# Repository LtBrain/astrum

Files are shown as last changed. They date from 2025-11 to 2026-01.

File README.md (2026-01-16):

# **ASTRUM**
Astrum (2)  
Astrum is a full robot designed for Science Olympiad's Robot Tour Event (2025-2026). It is designed to follow a predetermined path to navigate a maze and manipulate a water bottle to specific points on the floor. It is equipped with dual GA25 motors, a controller board (Aero), wheel encoders and an IMU to keep track of orientation. These features allow Astrum to quickly navigate the predetermined path efficiently and accurately with a PID loop controlling robot turning and motor speed.  
<br><br>
Astrum was created for the purpose of "placing" at the Mid-Hudson Valley Regionals competition, and to secure Nanuet a medal. Additionally, it serves as an educational tool for other students interested in robotics and control systems. It is able to be programmed in C, as well as Arduino, making it very effective for learning embedded software. This is also practice for myself, testing my design skills with both the hardware, and efficiently programming software to run on said board.  
  
## PCB
  

## Wiring Diagram 
wirediagram drawio
  
## BOM
Here's the BOM:  

 |Item #|Name                                       |Link                                     |Amount               |Cost   |
|------|-------------------------------------------|-----------------------------------------|---------------------|-------|
|1     |PCB + Assembly + Shipping                  |jlcpcb.com                               |1 order (2 boards)   |$170.40|
|2     |25GA-370 Brushed Motors                    |https://www.aliexpress.us/item/3256807346702379.html?|2                    |$12.94 |
|3     |Alinan AS5600 Encoder Boards               |https://www.aliexpress.us/item/3256809413529733.html?                              |1 pack (5 Encoders)  |$6.09 |
|4     |STEMMA QT to Male Header Cable             |https://www.aliexpress.com/item/3256805529535394.html?    |2                    |$2.78 |
|5     |2800 mAh AA NIMH Batteries                 |https://www.aliexpress.com/item/3256808440628751.html?                     |1 pack (12 Batteries)|$7.67 |
|6     |4 x AA Battery Holder                      |https://www.aliexpress.com/item/2255799895517935.html?     |2                    |$1.90  |
|7     |M3 16mm SHCS                               |M3 SHCS link                             |50                   |Paid by me  |
|8     |BaneBots T6 Wheel, 2-3/8" x 0.6", Hub Mount|https://banebots.com/t61p-242bp/         |2                    |$6.60  |
|9     |MF128ZZ Bearings - 8mm x 12mm x 3.5mm      |https://www.aliexpress.com/item/3256807566213882.html?                      |1 pack (8 bearings) |$6.10  |
|10    |Polulu 1/2 Inch Metal Ball Caster Wheels   |https://www.aliexpress.com/item/3256808387820251.html?     |4                    |$4.63 |
|11    |Pin Headers                                |https://www.aliexpress.com/item/2255800801798474.html?    |10                    |$1.69  |
|      |                                           |                                         |                     |Total: |
|      |                                           |                                         |                     |$220.80|
 
https://github.com/LtBrain/astrum/blob/main/Astrum%20BOM%20-%20Sheet1.csv

This covers the total sum of all the major parts.  

There is a more in depth BOM for the PCB assembly components itself: [BOM-astrum-JLCPCB Assembly Order.xls](https://github.com/user-attachments/files/23870804/BOM-astrum-JLCPCB.Assembly.Order.xls)  
  
REVIEWERS: Do note that I am aware of the high PCB fabrication costs + shipping, but this is the cheapest I could find it for (at JLCPCB). Additionally, the global standard direct shipping option will not work for this board. Sadly, JLCPCB requires the purchase to be under 59.99 dollars, which this board exceeds. This is why it got so expensive. Also do note that I have optimized my BOMs to be as cheap as possible to lower the amount of money spent by Hackclub.

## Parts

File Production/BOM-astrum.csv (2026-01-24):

Comment | Designator | Footprint | LCSC | Quantity
100nF | C11,C15,C16,C17,C19,C21,C4,C5,C6 | C_0603_1608Metric | C14663 | 9
100nF | C22 | C_0402_1005Metric | C1525 | 1
10k | R10,R8,R9 | R_0603_1608Metric | C25804 | 3
18pF | C7,C8 | C_0603_1608Metric | C1647 | 2
1uF | C12,C13,C9 | C_0603_1608Metric | C15849 | 3
2.2uF | C2 | C_0402_1005Metric | C12530 | 1
2.2uF | C1 | C_0603_1608Metric | C23630 | 1
22uF | C18,C20 | CP_Elec_4x5.4 | C3356 | 2
25mHz | Y2 | Crystal_SMD_3225-4Pin_3.2x2.5mm | C9006 | 1
30k | R3,R4 | R_0603_1608Metric | C22984 | 2
4.7k | R6 | R_0603_1608Metric | C23162 | 1
4.7uF | C10,C3 | C_0603_1608Metric | C19666 | 2
5.1k | R1,R2 | R_0603_1608Metric | C23186 | 2
Conn_01x04_MountingPin | J5,J6 | JST_SH_SM04B-SRSS-TB_1x04-1MP_P1.00mm_Horizontal | C160404 | 2
DRV8871DDA | U8,U9 | Texas_HTSOP-8-1EP_3.9x4.9mm_P1.27mm_EP2.95x4.9mm_Mask2.4x3.1mm_ThermalVias | C75864 | 2
LDL212PV33R | U2 | DFN_V33R_STM | C2969892 | 1
LSM6DSR | U6 | LGA_M6DSR_STM | C784817 | 1
Micro_SD_Card | J2 | microSD_HC_Wuerth_693072010801 | C5912397 | 1
NSR0530HT3G | D3 | D_SOD-323 | C191023 | 1
STM32H523CEUx | U1 | QFN-48-1EP_7x7mm_P0.5mm_EP5.6x5.6mm | C26082147 | 1
TS-1088-AR02016 | SW1,SW2 | SW-SMD_L3.9-W3.0-P4.45 | C720477 | 2
USBLC6-2SC6 | U3 | SOT-23-6 | C7519 | 1
USB_C_Receptacle_USB2.0_16P | J1 | USB_C_Receptacle_JAE_DX07S016JA1R1500 | C3197885 | 1
W25Q32JVSS | U4 | SOIC-8_5.3x5.3mm_P1.27mm | C97521 | 1
Conn_01x10_Pin | J8 | PinHeader_1x10_P2.54mm_Vertical |  | 1
Conn_01x10_Pin | J7 | PinHeader_1x10_P2.54mm_Vertical |  | 1
Conn_01x05_Pin | J10 | PinHeader_1x05_P2.54mm_Vertical |  | 1
Screw_Terminal_01x02 | J11 | TerminalBlock_bornier-2_P5.08mm |  | 1
Screw_Terminal_01x02 | J3 | TerminalBlock_bornier-2_P5.08mm |  | 1
Conn_01x05_Pin | J9 | PinHeader_1x05_P2.54mm_Vertical |  | 1

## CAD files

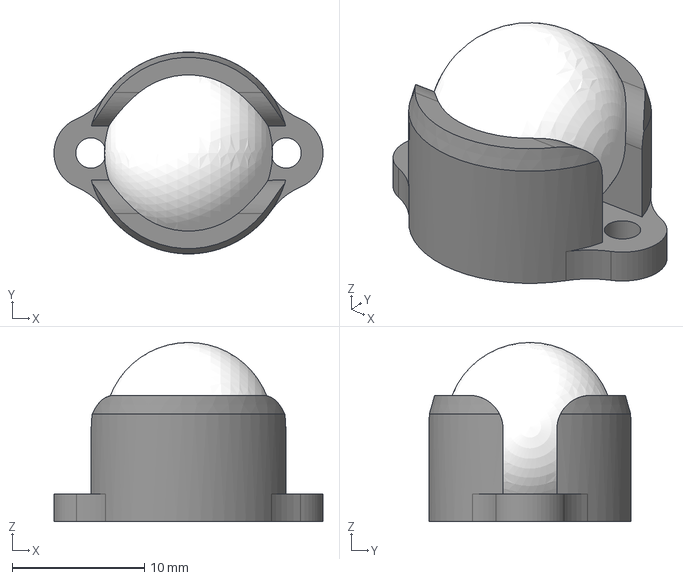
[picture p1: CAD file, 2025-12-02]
Production/3D Printed Parts/Motor_Mount.step
20.3 x 15.2 x 13.5 mm

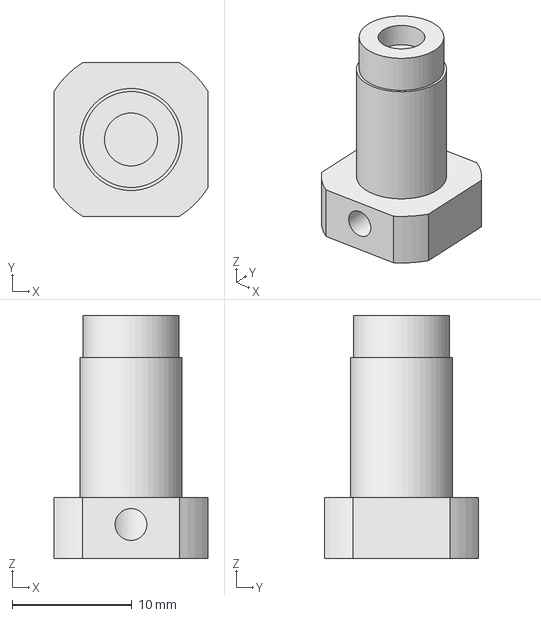
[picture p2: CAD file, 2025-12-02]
Production/3D Printed Parts/Motor_Hub.step
12.8 x 12.8 x 20.3 mm

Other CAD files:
Production/3D Printed Parts/Front_Plate.step
Production/3D Printed Parts/Bottom_Plate.step
Production/3D Printed Parts/Sensor_Hub.step
Production/3D Printed Parts/Wall_Plate.step

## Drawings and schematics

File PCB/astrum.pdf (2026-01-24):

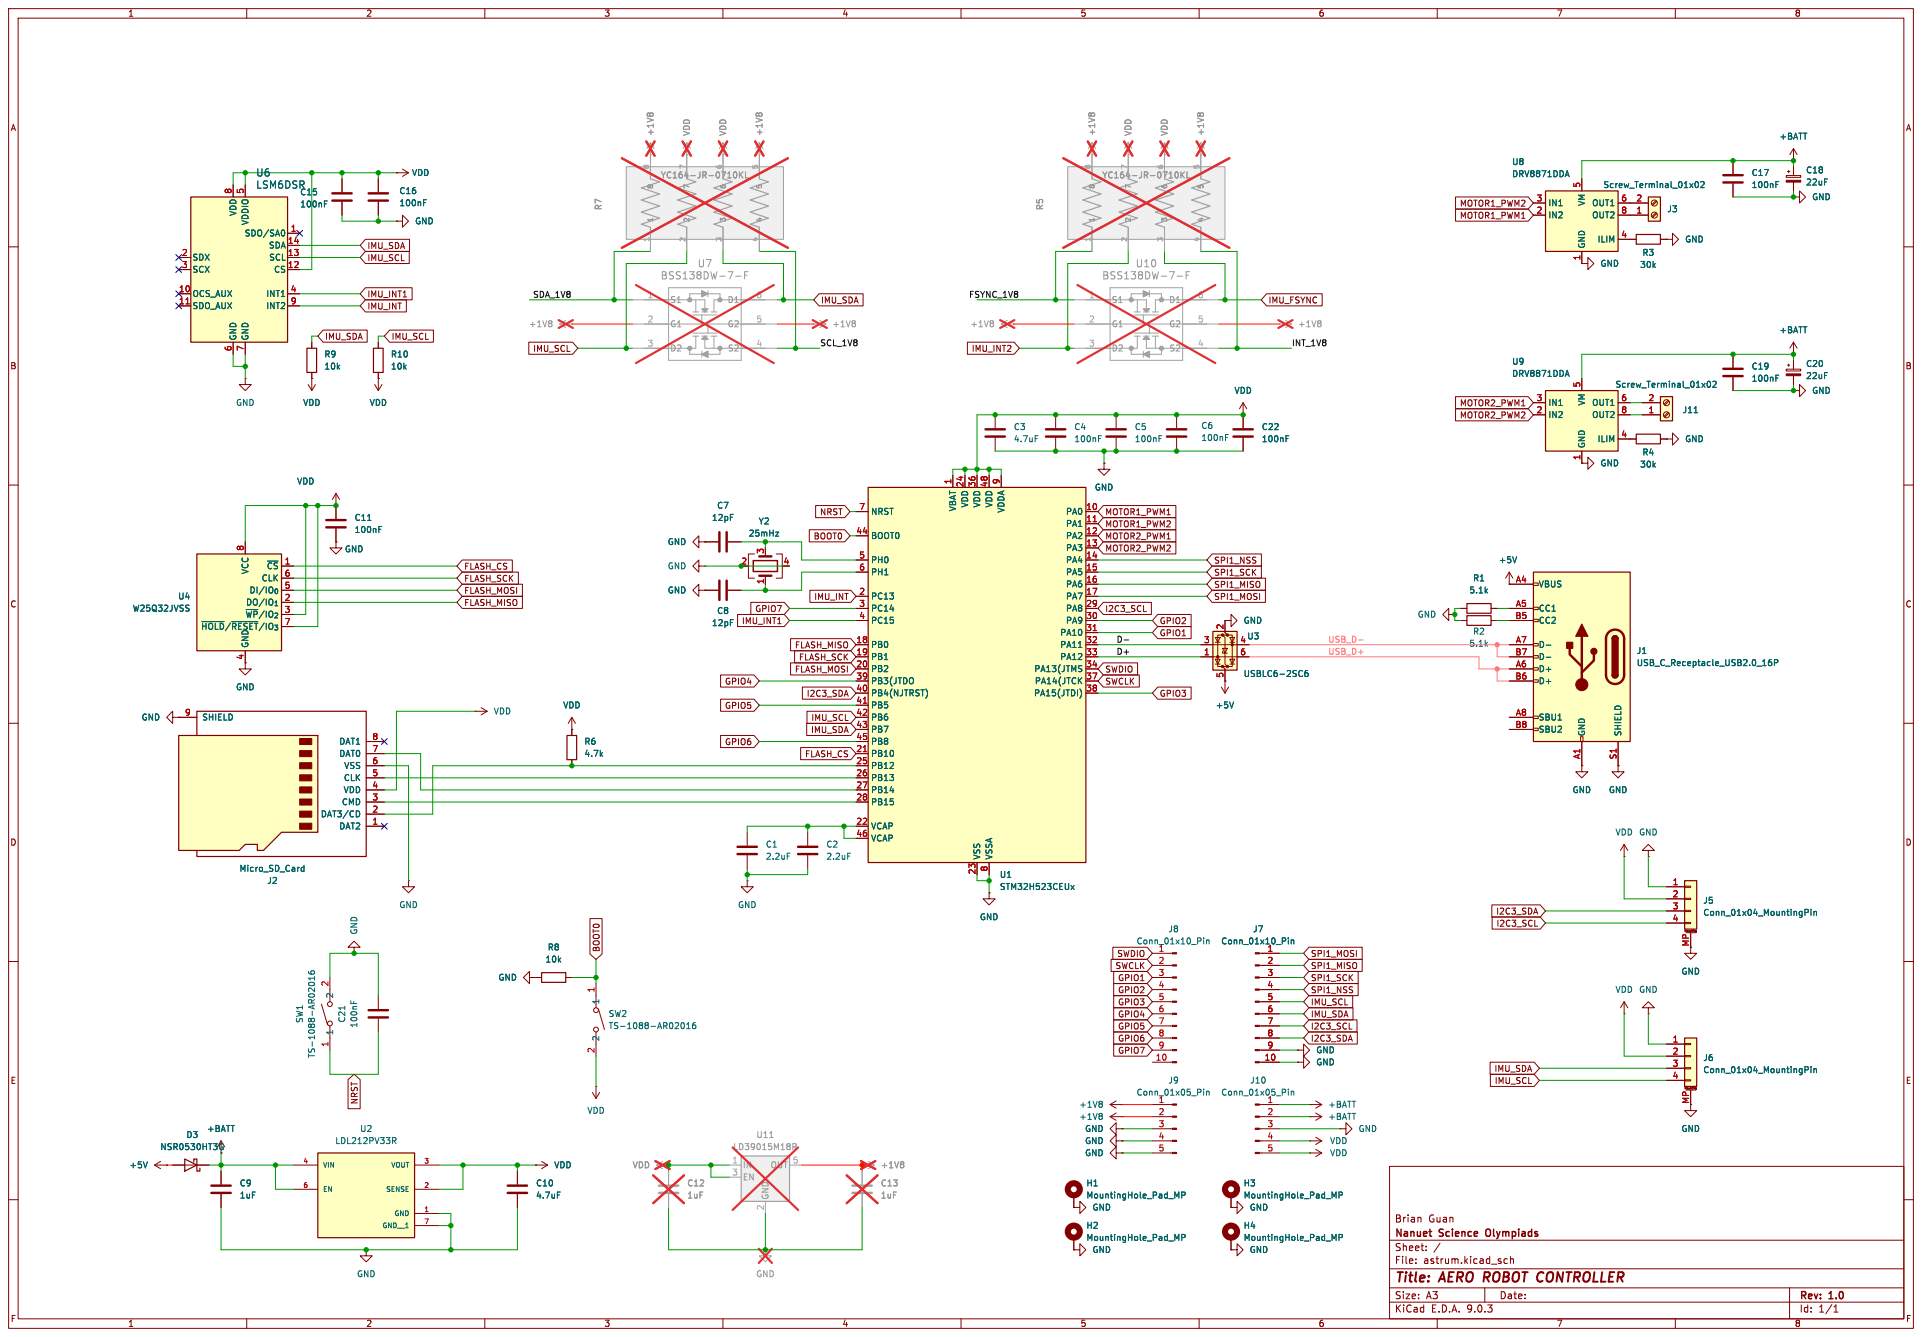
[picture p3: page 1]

7 SDO/SA0 1 SDA 14 SCL 13 CS 12

1 VDD 24 VDD 36 VSS 23 VDD 48 VSSA

9 PA0 10 PA1 11 PA2 12 PA3 13 PA4 14 PA5 15 PA6 16 PA7 17 PA8 29 PA9 30 PA10 31 PA11 32 PA12 33 PA13(JTMS 34 PA14(JTCK 37 PA15(JTDI) 38GND GND GND GND

~{CS}1 CLK 6 DI/IO_{0}5 DO/IO_{1}2 ~{WP}/IO_{2} 3 ~{HOLD}/~{RESET}/IO_{3} 7 VCC

Id: 1/1 Title: AERO ROBOT CONTROLLER

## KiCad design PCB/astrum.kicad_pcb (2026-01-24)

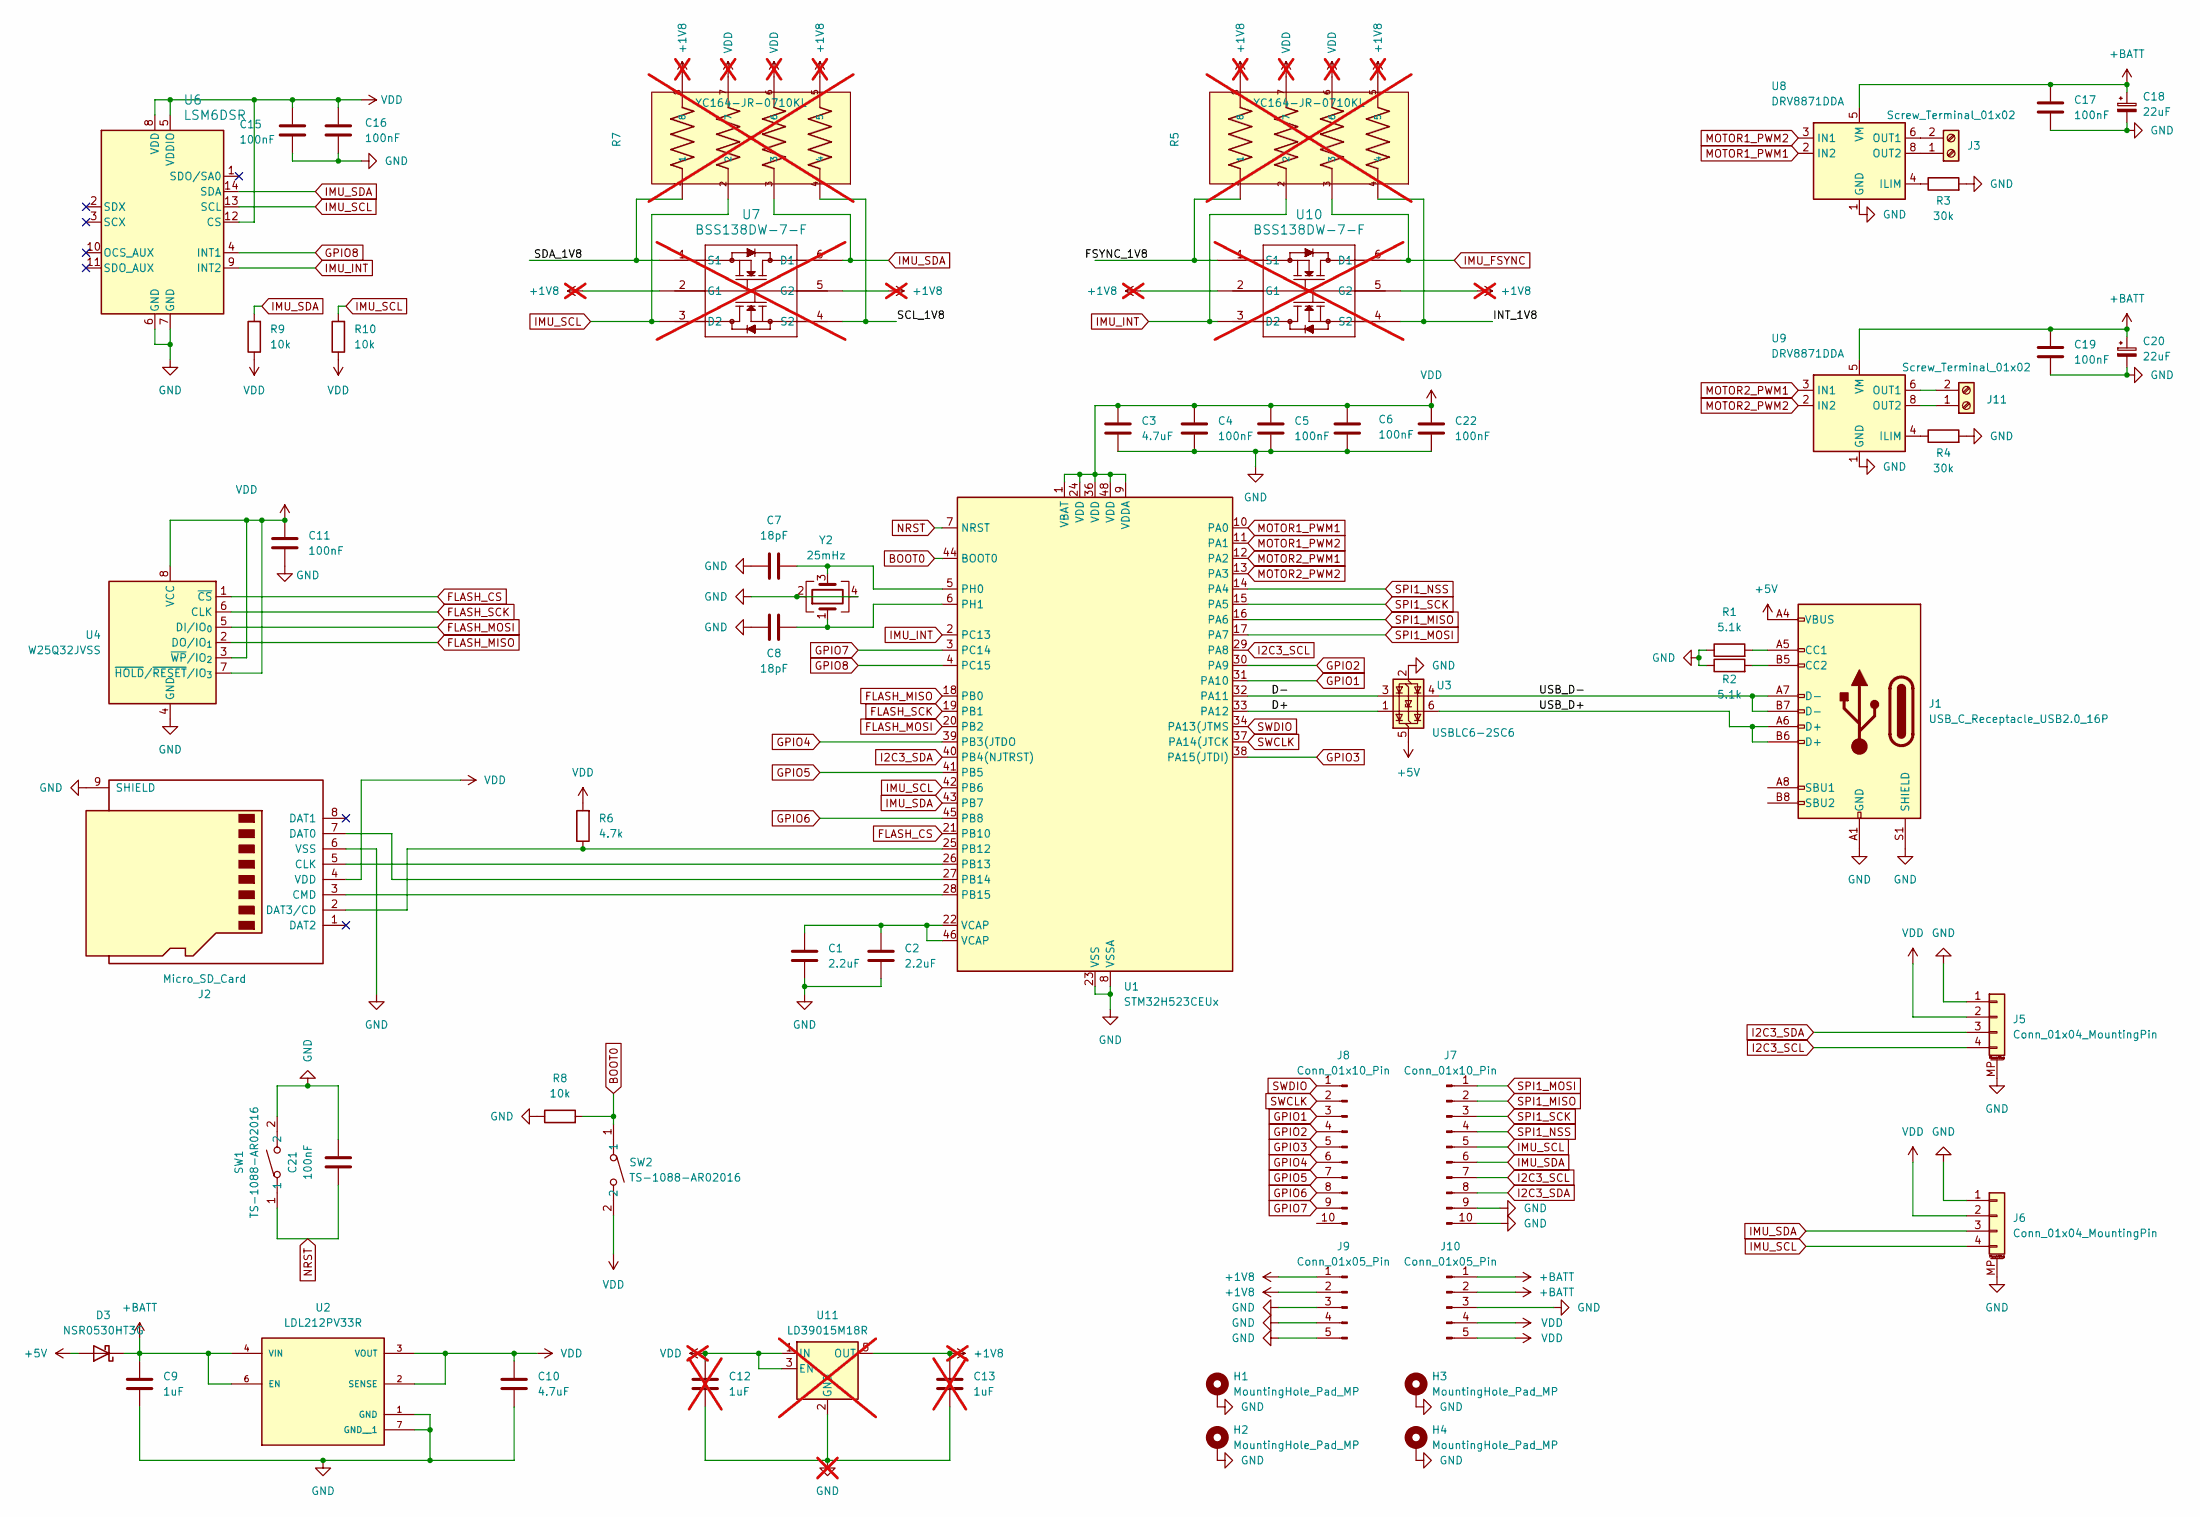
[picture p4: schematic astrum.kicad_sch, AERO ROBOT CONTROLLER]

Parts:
C1: 2.2uF; C_0603_1608Metric
C2: 2.2uF; C_0402_1005Metric
C3, C10: 4.7uF; C_0603_1608Metric
C4, C5, C6, C11, C15, C16, C17, C19, C21: 100nF; C_0603_1608Metric
C7, C8: 18pF; C_0603_1608Metric
C9: 1uF; C_0603_1608Metric
C12, C13: 1uF; C_0603_1608Metric; not fitted
C18, C20: 22uF; CP_Elec_4x5.4
C22: 100nF; C_0402_1005Metric
D3: NSR0530HT3G; D_SOD-323
H1, H2, H3, H4: MountingHole_Pad_MP; MountingHole_2.2mm_M2_ISO7380_Pad
J1: USB_C_Receptacle_USB2.0_16P; USB_C_Receptacle_JAE_DX07S016JA1R1500
J2: Micro_SD_Card; microSD_HC_Wuerth_693072010801
J3, J11: Screw_Terminal_01x02; TerminalBlock_bornier-2_P5.08mm
J5, J6: Conn_01x04_MountingPin; JST_SH_SM04B-SRSS-TB_1x04-1MP_P1.00mm_Horizontal
J7, J8: Conn_01x10_Pin; PinHeader_1x10_P2.54mm_Vertical
J9, J10: Conn_01x05_Pin; PinHeader_1x05_P2.54mm_Vertical
R1, R2: 5.1k; R_0603_1608Metric
R3, R4: 30k; R_0603_1608Metric
R5, R7: YC164-JR-0710KL; RESCAXE80P320X160X70-8N; PARTREV 9; not fitted
R6: 4.7k; R_0603_1608Metric
R8, R9, R10: 10k; R_0603_1608Metric
SW1, SW2: TS-1088-AR02016; SW-SMD_L3.9-W3.0-P4.45; LCSC Part C720477
U1: STM32H523CEUx; QFN-48-1EP_7x7mm_P0.5mm_EP5.6x5.6mm
U2: LDL212PV33R; DFN_V33R_STM; PARTREV 5
U3: USBLC6-2SC6; SOT-23-6
U4: W25Q32JVSS; SOIC-8_5.3x5.3mm_P1.27mm
U6: LSM6DSR; LGA_M6DSR_STM
U7, U10: BSS138DW-7-F; SOT363_DIO; not fitted
U8, U9: DRV8871DDA; Texas_HTSOP-8-1EP_3.9x4.9mm_P1.27mm_EP2.95x4.9mm_Mask2.4x3.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
U11: LD39015M18R; SOT-23-5; not fitted
Y2: 25mHz; Crystal_SMD_3225-4Pin_3.2x2.5mm

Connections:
+1V8: C13.1, J9.1, J9.2, R5.5, R5.8, R7.5, R7.8, U7.2 (G1), U7.5 (G2), U10.2 (G1), U10.5 (G2), U11.5 (OUT)
+5V: D3.2 (A), J1.A4 (VBUS), J1.A9 (VBUS), J1.B4 (VBUS), J1.B9 (VBUS), U3.5 (VBUS)
+BATT: C9.1, C17.1, C18.1, C19.1, C20.1, D3.1 (K), J10.1, J10.2, U2.4 (VIN), U2.6 (EN), U8.5 (VM), U9.5 (VM)
/D+: U1.33 (PA12), U3.1 (I/O1)
/D-: U1.32 (PA11), U3.3 (I/O2)
/FSYNC_1V8: R5.1, U10.1 (S1)
/INT_1V8: R5.4, U10.4 (S2)
/SCL_1V8: R7.4, U7.4 (S2)
/SDA_1V8: R7.1, U7.1 (S1)
/USB_D+: J1.A6 (D+), J1.B6 (D+), U3.6 (I/O1)
/USB_D-: J1.A7 (D-), J1.B7 (D-), U3.4 (I/O2)
BOOT0: R8.2, SW2.1, U1.44 (BOOT0)
FLASH_CS: U1.21 (PB10), U4.1 (~CS)
FLASH_MISO: U1.18 (PB0), U4.2 (DO/IO_{1})
FLASH_MOSI: U1.20 (PB2), U4.5 (DI/IO_{0})
FLASH_SCK: U1.19 (PB1), U4.6 (CLK)
GND: C1.2, C2.2, C3.2, C4.2, C5.2, C6.2, C7.1, C8.1, C9.2, C10.2, C11.2, C12.2, C13.2, C15.2, C16.2, C17.2, C18.2, C19.2, C20.2, C21.2, C22.2, H1.MP, H2.MP, H3.MP, H4.MP, J1.A1 (GND), J1.A12 (GND), J1.B1 (GND), J1.B12 (GND), J1.S1 (SHIELD), J2.6 (VSS), J2.9 (SHIELD), J5.1, J5.MP (MountPin), J6.1, J6.MP (MountPin), J7.9, J7.10, J9.3, J9.4, J9.5, J10.3, R1.1, R2.1, R3.2, R4.2, R8.1, SW1.2, U1.8 (VSSA), U1.23 (VSS), U1.35 (VSS), U1.47 (VSS), U1.49 (VSS), U2.1 (GND), U2.7 (GND__1), U3.2 (GND), U4.4 (GND), U6.6 (GND), U6.7 (GND), U8.1 (GND), U8.7 (GND), U8.9 (GND), U9.1 (GND), U9.7 (GND), U9.9 (GND), U11.2 (GND), Y2.2, Y2.4
GPIO1: J8.3, U1.31 (PA10)
GPIO2: J8.4, U1.30 (PA9)
GPIO3: J8.5, U1.38 (PA15(JTDI))
GPIO4: J8.6, U1.39 (PB3(JTDO)
GPIO5: J8.7, U1.41 (PB5)
GPIO6: J8.8, U1.45 (PB8)
GPIO7: J8.9, U1.3 (PC14)
GPIO8: U1.4 (PC15), U6.4 (INT1)
I2C3_SCL: J5.4, J7.7, U1.29 (PA8)
I2C3_SDA: J5.3, J7.8, U1.40 (PB4(NJTRST))
IMU_FSYNC: R5.3, U10.6 (D1)
IMU_INT: R5.2, U1.2 (PC13), U6.9 (INT2), U10.3 (D2)
IMU_SCL: J6.4, J7.5, R7.2, R10.2, U1.42 (PB6), U6.13 (SCL), U7.3 (D2)
IMU_SDA: J6.3, J7.6, R7.3, R9.2, U1.43 (PB7), U6.14 (SDA), U7.6 (D1)
MOTOR1_PWM1: U1.10 (PA0), U8.2 (IN2)
MOTOR1_PWM2: U1.11 (PA1), U8.3 (IN1)
MOTOR2_PWM1: U1.12 (PA2), U9.3 (IN1)
MOTOR2_PWM2: U1.13 (PA3), U9.2 (IN2)
NRST: C21.1, SW1.1, U1.7 (NRST)
unnamed: C1.1, C2.1, U1.22 (VCAP), U1.46 (VCAP)
unnamed: J1.A5 (CC1), R1.2
unnamed: J1.B5 (CC2), R2.2
unnamed: J2.5 (CLK), U1.26 (PB13)
unnamed: J2.3 (CMD), U1.28 (PB15)
unnamed: J2.7 (DAT0), U1.27 (PB14)
unnamed: J2.2 (DAT3/CD), R6.1, U1.25 (PB12)
unnamed: J3.1, U8.8 (OUT2)
unnamed: J3.2, U8.6 (OUT1)
unnamed: J11.1, U9.8 (OUT2)
unnamed: J11.2, U9.6 (OUT1)
unnamed: C7.2, U1.5 (PH0), Y2.3
unnamed: C8.2, U1.6 (PH1), Y2.1
unnamed: R3.1, U8.4 (ILIM)
unnamed: R4.1, U9.4 (ILIM)
SPI1_MISO: J7.2, U1.16 (PA6)
SPI1_MOSI: J7.1, U1.17 (PA7)
SPI1_NSS: J7.4, U1.14 (PA4)
SPI1_SCK: J7.3, U1.15 (PA5)
SWCLK: J8.2, U1.37 (PA14(JTCK)
SWDIO: J8.1, U1.34 (PA13(JTMS)
VDD: C3.1, C4.1, C5.1, C6.1, C10.1, C11.1, C12.1, C15.1, C16.1, C22.1, J2.4 (VDD), J5.2, J6.2, J10.4, J10.5, R5.6, R5.7, R6.2, R7.6, R7.7, R9.1, R10.1, SW2.2, U1.1 (VBAT), U1.9 (VDDA), U1.24 (VDD), U1.36 (VDD), U1.48 (VDD), U2.2 (SENSE), U2.3 (VOUT), U4.3 (~WP/IO_{2}), U4.7 (~HOLD/~RESET/IO_{3}), U4.8 (VCC), U6.5 (VDDIO), U6.8 (VDD), U6.12 (CS), U11.1 (IN), U11.3 (EN)

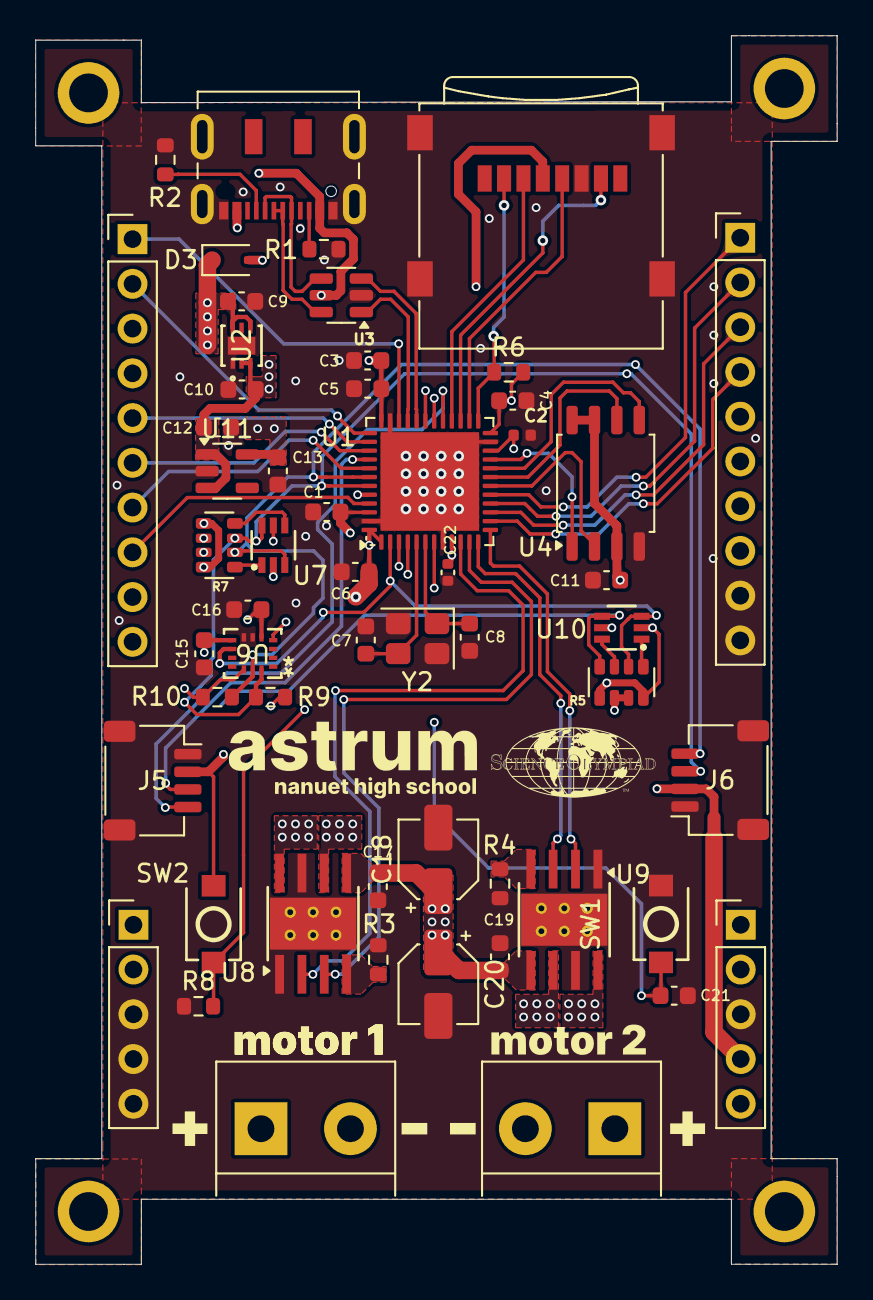
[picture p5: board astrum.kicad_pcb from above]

Board: 4 copper layers, 45.5 x 69.7 mm, 59 parts (0 on the bottom side), 58 nets.

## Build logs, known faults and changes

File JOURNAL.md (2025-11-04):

<!--
  ===================    !!READ THIS NOTICE!!   ====================
  DO NOT edit this file manually. Your changes WILL BE OVERWRITTEN!
  This journal is auto generated and updated by Hack Club Blueprint.
  To edit this file, please edit your journal entries on Blueprint.
  ==================================================================
-->

## 10/11/2025 9 PM - Planning and Schematic!  

I started out on my design with some rough knowledge on what I was going to use for this board. I had previously designed boards with the STM32H5 series, so I chose these as my microcontroller. This is a pretty solid choice for several reasons:

- 	Good documentation from STMicro (AN5711 comes with schematic diagrams)
- 	Lots of IO and interfaces to support the functionality on my board
- 	Is pretty cheap
-   Has lots of power, crucial for my control systems
-   STM32CubeMX makes configuration easy

With that determined, I began my KiCad project with the basic functionalities needed for the chip, such as decoupling capacitors and power rails. It was also at this time that I began to use CubeMX to determine which pins I should label for later peripheral usage, such as SPI, I2C and PWM from the timers: 

## 10/11/2025 10 PM - Power System & Drivers  

After sorting out the basic STM32 schematic, along with USB and storage, I decided to focus on my power supply. This board will primarily run on a 3v3 logic level, so I'll use the LDL212PV33R, a LDO that's really efficient with a 3.3v output @ 1.2 amps. Here's the circuit for that: 
I had to add a Schottky on the input because I didn't want backfeed to happen on my computer's USB port, just in case I accidentally have a battery pack and USB connected. 

After sorting my main power out, I moved onto my 2 motor drivers. This took a lot longer than expected, mainly because I got distracted by all the options out there. I had originally chosen the TB6612 from Toshiba, as this single IC would be able to control both motors bidirectionally. However, I felt that the simpler DRV8871 would be a better fit, as I could afford the space, and it made more sense in my mind to have the 2 chips spread out to dissipate more heat. TI also provides great documentation for these chips, sealing the deal. The schematic that I worked out looks like this 

These chips are H-Bridges, so they are each capable of powering 1 brushed DC motor. Additionally, they use PWM to control the speed of attached motors, with 2 inputs on each one. Sending a signal on one input makes it spin a certain, controllable speed in one direction, and the other input does the same for the other direction. This means that I will have to set up a total of 4 PWM generation channels on the STM32 with CubeMX: 

## 10/12/2025 12 PM - Schematics for the IMU  

There were a few IMU (inertial measurement unit) choices that I looked into, such as the Bosch BNO055, but I ultimately settled on the ICM-20948 from TDK Invensense. This chip is very accurate and low power, which is perfect for this PCB, as the batteries might be quickly depleted when 2 motors are used. 


However, this chip comes with a con: it uses a 1v8 logic level, which is not directly compatible with the STM32's 3v3 logic level. This requires a way to shift the signal from 1v8 max to 3v3, in both ways. I chose to do this with 2 BSS138 MOSFETs, as the signal lines won't be at very high speeds. For this IMU, I will be using I2C for simplicity.

Figuring out the ideal mosfets and IMU did take a lot of digging through datasheets, but did yield some useful information. This chip has an auxiliary I2C bus and FSYNC pin to add other components. However, in the case of this board, I really don't need any other sensors besides the IMU for odometry, so I'll just set this to no connect.  

## 10/12/2025 8 PM - Routing the PCB  

Now that the schematic is pretty much done, I started the PCB routing. The first thing I did was placing the decoupling capacitors for the STM32: 
The decoupling caps must be placed close to the VDD pins to reduce jitter on the supply, and should each have a close connection to ground to help with return currents. This board uses a 4 layer stackup, in Signal-Ground-Power-Signal configuration. I also placed the 25 mHz crystal in a similar fashion.

Moving on, I decided to route the USBC port. This will be used for programming and debug later, so it's crucial that this is done correctly. For this connector, I will be using a ESD chip to protect the single port against any static discharge, which could damage both my STM32 and the LDO regulators that supply power: 



After routing the USB port, I moved on to the SD card slot: 
I'm using the SD card in SPI mode, which greatly reduces the amount of traces that I need to route, and the amount of programming I need to do down the line, especially because this is not that important. I can easily program the flash over USB, but this method makes it easier for me to load configuration files on a SD card and into the robot on competition day.

Next, I focused on the SPI flash chip. This serves as an intermediary between the internal flash on the STM32, and the SD card, and is where I will be storing program files that are too large for the internal flash. Additionally, this would be great for data logging to collect some control loop info. 



The last thing I did today was routing out the IMU. This was a bit difficult because of how small it was, and how many additional components it needed to function properly. The first order of business was placing the decoupling capacitors: 

With that sorted, it was time to figure out all of the power supply. I had not started this yet, because I wanted to figure out what the most optimal placing was, and with the IMU in place, I chose the upper left side of my board. Here, I routed the 3v3 and 1v8 regulators, using lots of ground pour and thicker traces to carry more current without thermal increases: 

Now that the LDOs were all set up, I focused on the 1v8 regulator. This regulator supplies the ICM-20498, so I routed that in. After this, I began to configure the logic shifters, creating compact groups like these to minimize space use: 

I set up 2 of these, and they require both 3v3 and 1v8 power to pull the signal lines up. This were most of the processing side components, and what was accomplished today allows me to focus all my attention on the drivers next time. 

## 10/13/2025 - Routing the PCB Day 2  

Last time, I left off at the processing side of routing. Today, I routed the 2 motor drivers. These H-Bridges have to relatively far away from the processing side of the board so that no odd EMI and inductance issues occur. On my board, I placed them around 1.2 cm away from any of the components connect to the STM32. What I ended up with looked like this: 
I tried to make this section compact so that I could have space for power headers on either side, so the electrolytic bulk caps are placed in between. I will also use copper pours here to carry more current. These motor drivers will receive power directly from the batteries, so I added some pin headers in the schematic to supply electricity: 



I also finished routing out 90 percent of the power layer traces, so this board is getting really close to production-ready. I might redesign the power layer later, as I don't have that many nets and could probably power the entire layer: 

The last thing I did was add and connect some connectivity/data pin headers for I/O.  

## 10/17/2025 - Fixed some PCB issues  

I widened the connection between the mounting pads and the actual board so fabrication would be easier: 

Routed the SWDIO and SWCLK pins to the headers: 

Routed all remaining, free GPIO pins to the headers: 

There are some odd DRC issues regarding aperture of the soldermask, so I'll ask around during a design review. Speaking of which, I sent the repo in the r/rocketry and Electrical Engineering Discord servers to get some feedback.  

## 10/27/2025 - CAD work?  

So, I'm back? Yea, the last couple of weeks were quite hectic (lots of AP stuff), but I finally got some CAD work done. The first thing I had to design was the baseplate for the robot chassis. It needs to have 2 slots for wheels to poke through for the drive, and mounting holes for all the electronics on board. 
This is what I came up with for now. It has 4 mounting holes for my controller board, and the 2 holes next to each wheel hole attach to the motor mounts. I went a bit further and did some assembly and design of the motor mounts and wheel hubs (I need to convert the D profile to a square profile for the wheel) 


## 11/4/2025 - CAD work? Pt.2  

So I'm back, and I pretty much finished the enclosure design. I essentially extruded a shell of the baseplate to get this:  and made this: 

Honestly, I thought this made it look a lot like a brick, so I added a slant on the front to add some aesthetics. This also has the added benefit of pushing/holding the water bottle at a lower point, so we don't have that many issues with the bottle's CG or tipping it over. . This also means that I had to tilt the screw holes so that the cover plate could easily screw in. After doing that, I moved on to the wheel wells. I already knew that the encoders would stick out a bit for easy access, so I made this arch on each side for access to the wheels, hub and encoder. 

Moving on to the encoder/hub, I designed these with a flanged bearing in mind. This just makes everything much more easy to assemble, so I ended up with this encoder holder.  The AS5600 board mounts onto the holes shown on the right side, which spaces it a perfect .5 mm away from the magnet in the center of the wheel. The other side has a section to allow the flange to sit flat. . 

With all of this done, I quickly threw together the battery box, which is a bit awkward because it needs to fit 2 4xAA battery packs on top of each other to provide the required amount of power. I ended up with something like this: 

After the battery box, I sketched and extruded the 2 cover pieces:  

Now that every part is complete, I started up the assembly of the entire robot. It was quite intuitive, and I had already thought of all the component positions. I decided to put the battery box right on top of the computer, because it already had mounting points on the base, which was definitely interesting. I ended up with this: 

I was able to spend a lot of time today because of Election Day (no school), so lots of progress was made.

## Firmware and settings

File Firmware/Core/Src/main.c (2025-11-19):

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
/* Includes ------------------------------------------------------------------*/

/* USER CODE BEGIN 2 */
//Drivers
#include "main.h"
#include "as5600.h"
#include "icm20948_api.h"
#include "drv8871.h"

//APIs
#include "PID.h"
/* USER CODE END 2 */

I2C_HandleTypeDef hi2c1;
I2C_HandleTypeDef hi2c3;

SPI_HandleTypeDef hspi2;
SPI_HandleTypeDef hspi3;

TIM_HandleTypeDef htim2;
TIM_HandleTypeDef htim6;

PCD_HandleTypeDef hpcd_USB_DRD_FS;

void SystemClock_Config(void);
void PeriphCommonClock_Config(void);
static void MX_GPIO_Init(void);
static void MX_SPI2_Init(void);
static void MX_SPI3_Init(void);
static void MX_USB_PCD_Init(void);
static void MX_I2C1_Init(void);
static void MX_TIM2_Init(void);
static void MX_TIM6_Init(void);
static void MX_I2C3_Init(void);
static void MX_FLASH_Init(void);

/* USER CODE BEGIN 3 */
AS5600_HandleTypeDef leftEncoder;
AS5600_HandleTypeDef rightEncoder;

#define ICM20948_I2C_ADDRESS 0x68 << 1  // Adjust based on AD0 pin

int8_t usr_write(const uint8_t addr, const uint8_t *data, const uint32_t len) {
    // Write 'len' bytes to register 'addr'
    HAL_StatusTypeDef status = HAL_I2C_Mem_Write(&hi2c1, ICM20948_I2C_ADDRESS, addr, I2C_MEMADD_SIZE_8BIT, (uint8_t *)data, len, 100);
    return status == HAL_OK ? 0 : -1;
}

int8_t usr_read(const uint8_t addr, uint8_t *data, const uint32_t len) {
    // Read 'len' bytes from register 'addr' into 'data'
    HAL_StatusTypeDef status = HAL_I2C_Mem_Read(&hi2c1, ICM20948_I2C_ADDRESS, addr, I2C_MEMADD_SIZE_8BIT, data, len, 100);
    return status == HAL_OK ? 0 : -1;
}

/* USER CODE END 3 */

volatile uint8_t timer6Flag = 0;

int main(void)
{
  /* MCU Configuration--------------------------------------------------------*/
  /* Reset of all peripherals, Initializes the Flash interface and the Systick. */
  HAL_Init();
  SystemClock_Config();

  /* Configure the peripherals common clocks */
  PeriphCommonClock_Config();

  /* Initialize all configured peripherals */
  MX_GPIO_Init();
  MX_SPI2_Init();
  MX_SPI3_Init();
  MX_USB_PCD_Init();
  MX_I2C1_Init();
  MX_TIM2_Init();
  MX_TIM6_Init();
  MX_I2C3_Init();
  MX_FLASH_Init();
  
  /* USER CODE BEGIN 4 */

  HAL_TIM_Base_Start_IT(&htim6); 

  //AS5600 INIT
  leftEncoder.hi2c = &hi2c1;
  rightEncoder.hi2c = &hi2c3;

  uint16_t leftAngle, rightAngle;

  while (1)
  {
    if (timer6Flag) {
      timer6Flag = 0;

      AS5600_ReadAngle(&leftEncoder, &leftAngle);
      AS5600_ReadAngle(&rightEncoder, &rightAngle);

      float leftAngleDeg = (leftAngle * 360) / 4096;
      float rightAngleDeg = (rightAngle *360) / 4096;
    }
  }

  //ICM20948 INIT
  icm20948_return_code_t ret = ICM20948_RET_OK;
  icm20948_settings_t settings;
  icm20948_gyro_t gyro_data;
  icm20948_accel_t accel_data;

  // ret = icm20948_init(usr_read, usr_write, usr_delay_us);

  /* USER CODE END 4 */
  
}

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


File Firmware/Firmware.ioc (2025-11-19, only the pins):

Mcu.UserName=STM32H523CEUx
PA0.Signal=S_TIM2_CH1
PA1.Signal=S_TIM2_CH2
PA11.Signal=USB_DM
PA12.Signal=USB_DP
PA13(JTMS/SWDIO).Signal=DEBUG_JTMS-SWDIO
PA14(JTCK/SWCLK).Signal=DEBUG_JTCK-SWCLK
PA2.Signal=S_TIM2_CH3
PA3.Signal=S_TIM2_CH4
PA4.Signal=SPI1_NSS
PA5.Signal=SPI1_SCK
PA6.Signal=SPI1_MISO
PA7.Signal=SPI1_MOSI
PA8.Signal=I2C3_SCL
PB0.Signal=SPI3_MISO
PB1.Signal=SPI3_SCK
PB10.Signal=GPIO_Output
PB12.Signal=SPI2_NSS
PB13.Signal=SPI2_SCK
PB14.Signal=SPI2_MISO
PB15.Signal=SPI2_MOSI
PB2.Signal=SPI3_MOSI
PB4(NJTRST).Signal=I2C3_SDA
PB6.Signal=I2C1_SCL
PB7.Signal=I2C1_SDA
PC13.Signal=GPIO_Input
PH0-OSC_IN(PH0).Signal=RCC_OSC_IN
PH1-OSC_OUT(PH1).Signal=RCC_OSC_OUT

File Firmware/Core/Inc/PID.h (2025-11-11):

#include <stdio.h>
#include <stdlib.h>

#define TIME_STEP 0.01 

typedef struct {
    float kp; // Proportional gain
    float ki; // Integral gain
    float kd; // Derivative gain

    float integral;
    float previous_error;
    
    float output;
} PID_Constants;

PID_Constants PIDController(float kp, float ki, float kd) {
    PID_Constants pid = {kp, ki, kd, 0, 0, 0};
    return pid;
}

double PIDCalculate(PID_Constants *pid, double position, double setpoint) {
    double error = setpoint - position;
    
    // P term
    double P = pid->kp * error;

    // I term
    pid->integral += error * TIME_STEP;
    double I = pid->ki * pid->integral;

    // D term
    double D = pid->kd * (error - pid->previous_error) / TIME_STEP;

    // store error for next step
    pid->previous_error = error;

    // total output
    pid->output = P + I + D;
    return pid->output;
}

double getP(double P) {
    return(P);
};

double getI(double I) {
    return(I);
};

double getD(double D) {
    return(D);
};

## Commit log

2025-10-12 add stm32, basic peripherals
    [astrum.kicad_pcb, astrum.kicad_sch]
2025-10-12 add drv8871 drivers to the board
    [astrum.kicad_sch]
2025-10-12 add imu schematics
    [astrum.kicad_sch]
2025-10-13 route the processing side of the board
    [astrum.kicad_pcb]
2025-10-14 add the drv routing and header pins + power supply
    [astrum.kicad_pcb, astrum.kicad_sch]
2025-10-17 add more gpio header things
    [astrum.kicad_pcb, astrum.kicad_sch]
2025-10-17 fix the power plane and the mounting holes
    [astrum.kicad_pcb, astrum.kicad_sch]
2025-11-06 add firmware and cad stuff
    [astrum.kicad_pcb, astrum.kicad_sch]
2025-11-08 generate the cubemx project, add as5600 driver code
2025-11-09 add icm20948 driver
2025-11-09 add drv8871 motor helper?
2025-11-10 add PID controller
2025-11-11 some more pid?
2025-12-01 update production files
    [astrum.kicad_pcb, astrum.kicad_sch]
2025-12-02 actually push the bom
    [BOM-astrum.csv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]
2025-12-02 update bom to include new 1v8 regulator
    [BOM-astrum.csv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]
2025-12-02 Add BOM section with links to detailed resources
    Added a Bill of Materials (BOM) section to the README.
2025-12-02 Revise BOM section with item details and links
    Updated the BOM section with detailed item list and links.
2025-12-02 add production step files
    [BOM-astrum.csv, Bottom_Plate.step, Front_Plate.step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]
2025-12-02 Update Astrum BOM - Sheet1.csv
    [Astrum BOM - Sheet1.csv]
2025-12-03 final production files?
    [BOM-astrum.csv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]
2025-12-05 Revise BOM with new links and updated prices
    Updated links and costs for various components in the bill of materials.
2025-12-05 Revise Astrum BOM with new links and prices
    Updated item details and costs in the BOM.
    [Astrum BOM - Sheet1.csv]
2025-12-05 Update Astrum BOM with new item formatting
    [Astrum BOM - Sheet1.csv]
2025-12-06 Update README with PCB costs and BOM details
    Added notes regarding PCB fabrication costs and BOM optimization.
2025-12-14 make the board cheaper?
    [astrum.kicad_pcb, astrum.kicad_sch]
2025-12-14 fix oscillator
    [BOM-astrum.csv, astrum.kicad_pcb, astrum.kicad_sch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]
2025-12-14 Update BOM with shipping costs and total amount
2025-12-14 Revise BOM with updated costs and shipping
    Updated item costs and added shipping to PCB assembly.
    [Astrum BOM - Sheet1.csv]
2026-01-16 fix some dum vcap thingies
    [astrum.kicad_pcb, astrum.kicad_sch]
2026-01-24 update stuff again
    [BOM-astrum.csv, astrum.kicad_pcb, astrum.kicad_sch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]

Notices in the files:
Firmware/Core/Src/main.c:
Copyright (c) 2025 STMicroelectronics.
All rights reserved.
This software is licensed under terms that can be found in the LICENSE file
